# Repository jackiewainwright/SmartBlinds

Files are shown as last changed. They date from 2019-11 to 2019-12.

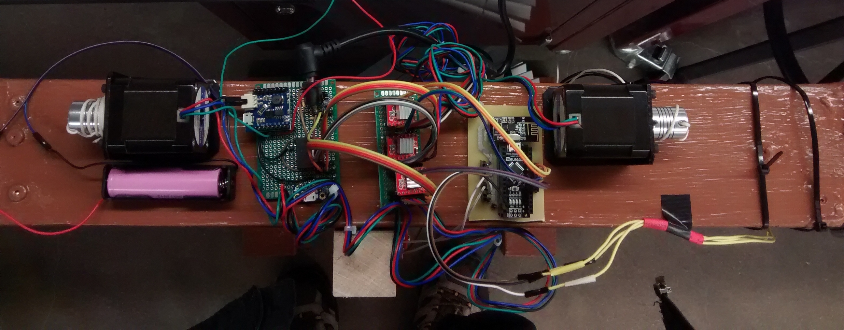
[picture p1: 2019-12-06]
hardware_photo.jpg

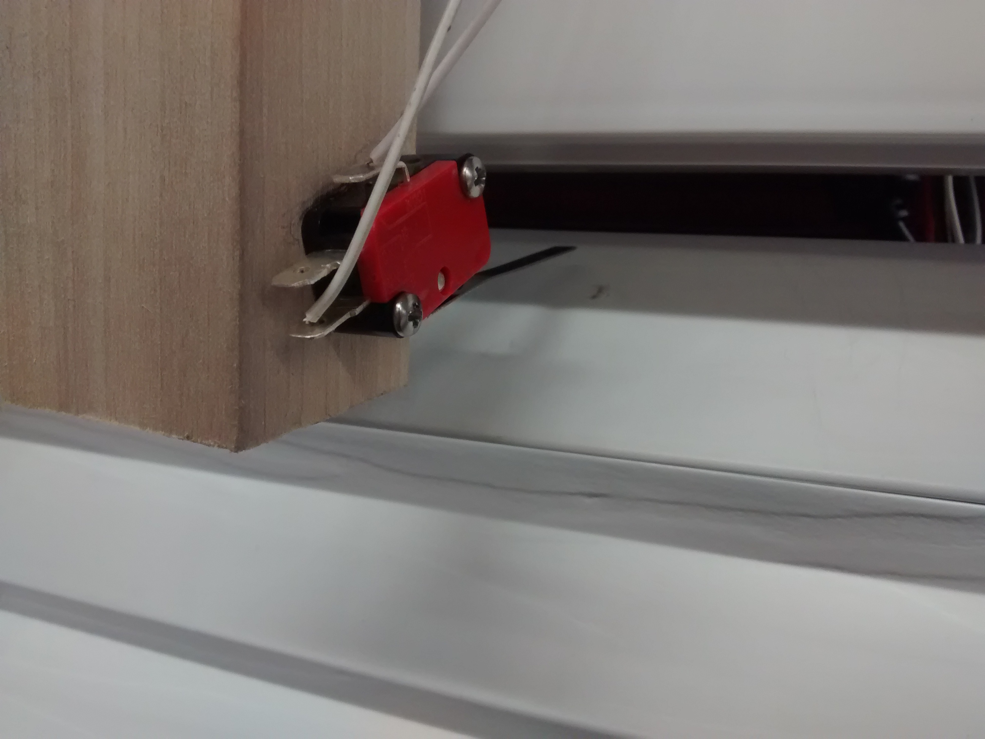
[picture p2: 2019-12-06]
switch_photo.jpg

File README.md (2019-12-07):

# SmartBlinds
A senior design project that has a mobile application that sends user preferences (time, light, temp) to a micro controller system. The micro controller system tells the blinds whether to go up or down based off input from the sensor subsystem. The micro controller controls the motors which raises blinds up/down and opens slats.

# Motors
File descriptions:
- motorhw: is an Eagle project that contains the PCB I printed. The PCB was only half used since it was printed before we switched motors. The half containing the Nano and transceiver is used, while the half containing motor drivers is unused. Pictures of the schematic and layouts are in motorhw\_schematic.png and motorhw\_layout.png. 
- hardware\_photo.jpg and switch\_photo.jpg: Pictures of the final products.
- motor\_demonstration.mov: Video of the blinds being lifted, lowered and rotated to their limits. 
- logic\_diagram.png and power\_diagram.png: Basic schematics made in Fritzing. These are kind of low-quality because I couldn't find files for every part. In the logic diagram, two jacks are shown; the top supplies 12V and the bottom supplies 5V. In the drivers, A1,A2,B1,B2 aren't connected; they each should be connected to a motor. In the power diagram, imagine the battery is a Li-Ion, replace the TP4056 with a TP5410, imagine it's on a protoboard instead of breadboard. 
- keiths\_program.ino: Program used by Keith on the nano. 
- my\_program.ino: Program used by me to develop and test the motor subsystem.
- additional_validation.pdf: Validation that I didn't put in the report. My bad

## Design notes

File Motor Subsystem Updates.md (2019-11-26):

9-25

Rough PCB design finished. However, we've decided to get a protoboard version working. For the final product, a protoboard will work. The only problem is reduced technical merit. 

9-30 

Finished proto board.

This proto board is split into 3 boards: nano board, motor board, and power board. 
* Nano board contains the nano, transceiver, multiple resistors for switches, and two transistors. 
* Motor board contains two motor drivers and three header rows providing an interface with the motors. 
* Power board contains the battery charger chip. It has headers connecting the battery, solar panel, and multiple power and ground connections. 

The nano board isn't soldered; it can easily, reliably, and more temporarily be connected with jumper wires. In the future, it may be soldered to become more reliable.

The motor board is fully soldered and tested, and it works.

The power board has the solar and battery components soldered. However, it doesn't have USB power connections soldered; this part may need minor design revisions first. 

Right now, we have a very solid option in the proto boards. There's no real need to get a PCB, except to increase technical merit and make it closer to a marketable product. 

10-14
We decided to change things up. The 28BYJs are pretty weak and lifting the blinds is too big a job for them. We bought NEMA-17s and drivers, and we'll use them to lift and probably rotate the blinds. 

10-22
Obtained the PCB finally. I got two copies in case one failed. The traces of one all work properly, so it seems like it'll work. I will solder female headers to attach the Nano and nRF transceiver. Currently I need surface-mount resistors, transistors, and capacitors, but if we go forward with the new motors the transistors and caps may not be necessary. 
If we replace the 28BYJ-48s with NEMA-17s, the right half of the board will be unnecessary, so I'll cut it off. 

10-27
Soldered power board together. 
Due to a miscommunication we didn't have a voltage booster chip. I bought a new battery-charging chip (TP5410) that boosts voltage as well. 

10-28
Tested the motor drivers. They can, in fact, run the motors. At max current, the drivers pull 12V 410mA, then deliver to the motor 1.05A per-phase. 

10-29
Soldered two motor drivers onto a protoboard. Put one motor on blinds, then tested whether it can lift half the blinds (successfully). Made video of motor lifting its share of blinds. 
The protoboard will be part of the final product. It'll have many jumpers connected to the power board and Arduino, but that's okay. The jumpers should be orderly enough to be more reliable than a breadboard. 

10-30
In lab, we drilled holes in the frame. One string is used for each side to lift the blinds, and they go through the holes to the top of the frame, where motors lift them. One shaft adaptor is put on each motor to attach the string.
It turned out we're missing a shaft adaptor, so we couldn't test rotation. We know it has enough torque because the 28BYJs did, and we'll implement this later. 

11-03
I accidentally burned out the battery charging board in a puff of smoke, so that's fun. However, I managed to test it enough to determine that the voltage boosting will be good enough (4.7V at 50mA), and it does charge the battery. I bought a new one and it'll ship on the 5th. 

11-19
The A4988 motor drivers burn out really easily, and I've had to buy 5 new ones. Made a new protoboard, fitted with female headers so I can add and replace driver boards whenever they burn out again.

11-24
Keith's motor program is complete and validated, and videos were made. The rotation is calibrated to within 5°.

11-25
The demo is tomorrow, and every part of the motor subsystem works.

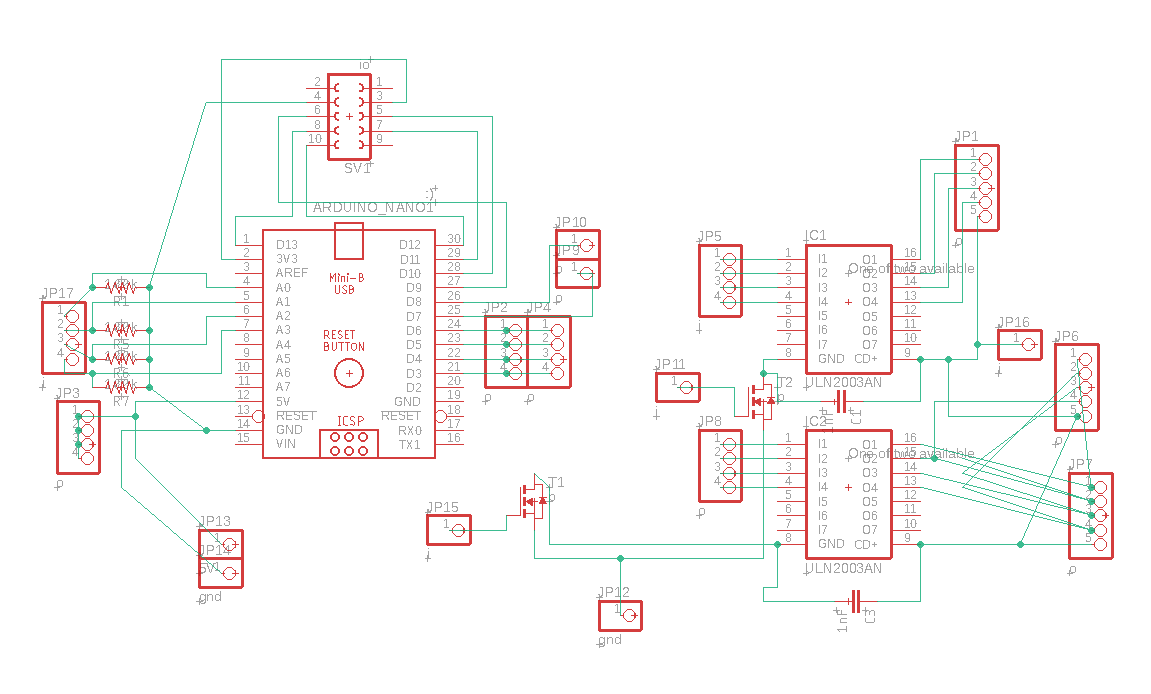
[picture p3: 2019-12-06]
motorhw_schematic.png

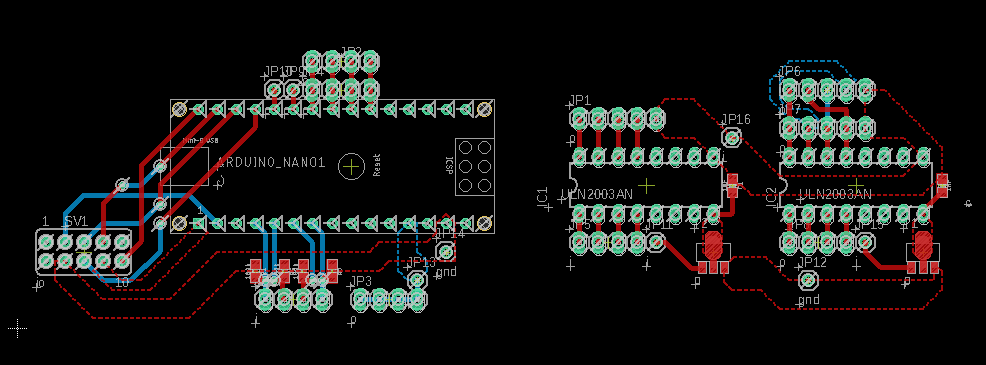
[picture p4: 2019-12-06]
motorhw_layout.png

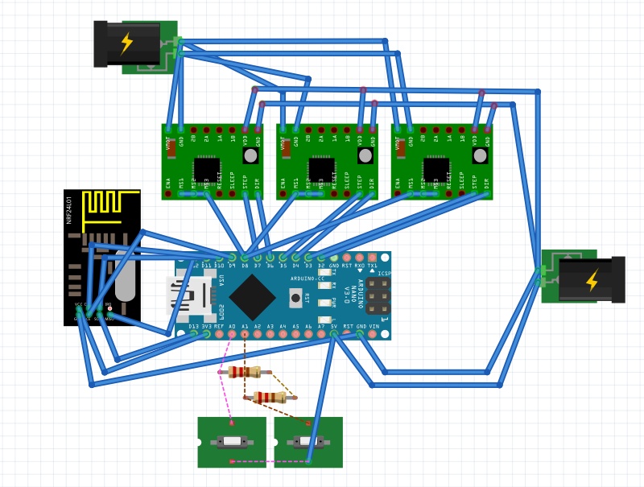
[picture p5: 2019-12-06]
logic_diagram.png

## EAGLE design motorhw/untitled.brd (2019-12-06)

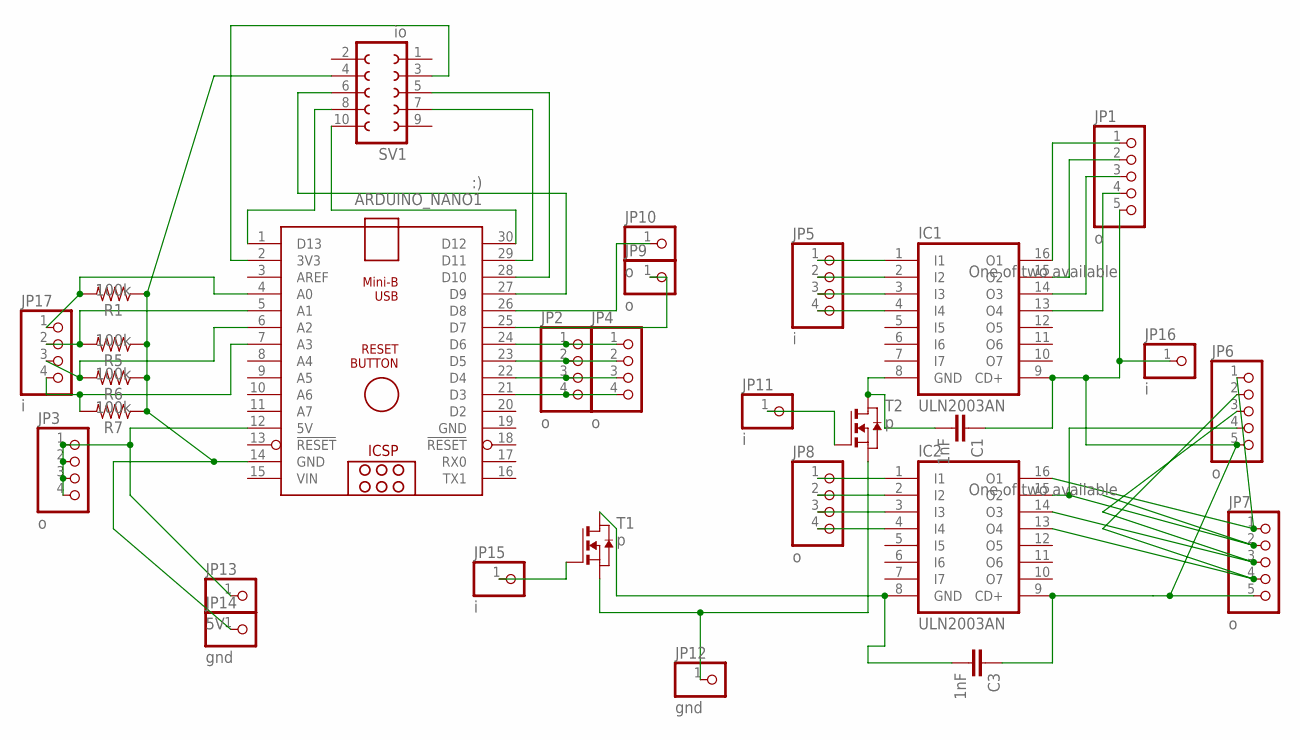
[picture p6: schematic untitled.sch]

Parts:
ARDUINO_NANO1: :); ARDUINO_NANO
C1, C3: 1nF; 0603
IC1, IC2: ULN2003AN; DIL16
JP1, JP6, JP7: o; 1X05
JP2, JP3, JP4, JP8: o; 1X04
JP5, JP17: i; 1X04
JP9, JP10: o; 1X01
JP11, JP15, JP16: i; 1X01
JP12, JP14: gnd; 1X01
JP13: 5V; 1X01
R1, R5, R6, R7: 100k; 0603
SV1: io; FE05-2
T1, T2: p; SOT89

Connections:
3V3: ARDUINO_NANO1.1 (D13), SV1.8
GND: ARDUINO_NANO1.19 (GND)
GND1: ARDUINO_NANO1.14 (GND), JP14.1, R1.1, R5.1, R6.1, R7.1, SV1.4
GND2: JP12.1, T1.3 (S), T2.3 (S)
LONGTHINGY: IC2.15 (O2), JP6.4, JP7.2
unnamed: ARDUINO_NANO1.4 (A0), JP17.1, R1.2
unnamed: ARDUINO_NANO1.21 (D3), JP2.4, JP4.4
unnamed: ARDUINO_NANO1.30 (D12), SV1.10
unnamed: IC2.16 (O1), JP6.1, JP7.1
unnamed: IC2.14 (O3), JP6.3, JP7.3
unnamed: IC2.13 (O4), JP6.2, JP7.4
unnamed: IC1.16 (O1), JP1.1
unnamed: IC1.15 (O2), JP1.2
unnamed: IC1.14 (O3), JP1.3
unnamed: IC1.13 (O4), JP1.4
unnamed: ARDUINO_NANO1.22 (D4), JP2.3, JP4.3
unnamed: ARDUINO_NANO1.25 (D7), JP9.1
unnamed: ARDUINO_NANO1.23 (D5), JP2.2, JP4.2
unnamed: ARDUINO_NANO1.29 (D11), SV1.7
unnamed: ARDUINO_NANO1.28 (D10), SV1.5
unnamed: ARDUINO_NANO1.27 (D9), SV1.6
unnamed: ARDUINO_NANO1.24 (D6), JP2.1, JP4.1
unnamed: ARDUINO_NANO1.2 (3V3), SV1.3
unnamed: IC1.1 (I1), JP5.1
unnamed: IC1.2 (I2), JP5.2
unnamed: IC1.3 (I3), JP5.3
unnamed: IC1.4 (I4), JP5.4
unnamed: IC2.1 (I1), JP8.1
unnamed: IC2.2 (I2), JP8.2
unnamed: IC2.3 (I3), JP8.3
unnamed: IC2.4 (I4), JP8.4
unnamed: ARDUINO_NANO1.26 (D8), JP10.1
unnamed: JP11.1, T2.1 (G)
unnamed: JP15.1, T1.1 (G)
unnamed: ARDUINO_NANO1.5 (A1), JP17.2, R5.2
unnamed: ARDUINO_NANO1.6 (A2), JP17.3, R6.2
unnamed: ARDUINO_NANO1.7 (A3), JP17.4, R7.2
ULN1GND: C1.2, IC1.8 (GND), T2.2 (D), T2.2@1 (D)
ULN2GND: C3.2, IC2.8 (GND), T1.2 (D), T1.2@1 (D)
VCC1: ARDUINO_NANO1.12 (5V), JP3.1, JP3.2, JP3.3, JP3.4, JP13.1
VCC2: C1.1, C3.1, IC1.9 (CD+), IC2.9 (CD+), JP1.5, JP6.5, JP7.5, JP16.1
VIN: ARDUINO_NANO1.15 (VIN)

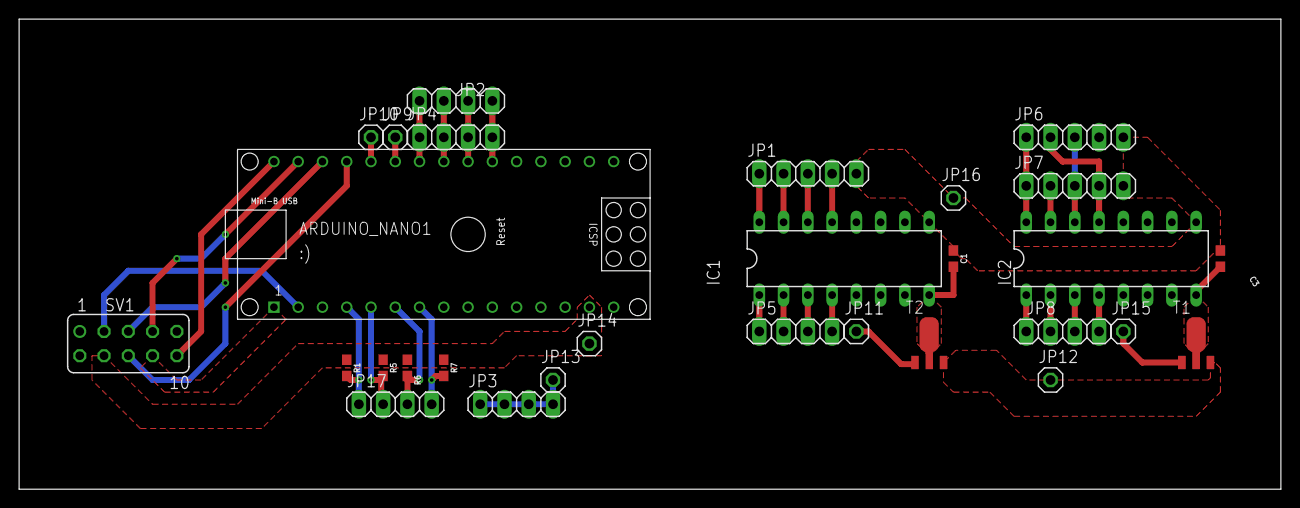
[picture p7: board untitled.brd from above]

Board: 2 copper layers, 132.1 x 49.2 mm, 29 parts (0 on the bottom side), 40 nets.

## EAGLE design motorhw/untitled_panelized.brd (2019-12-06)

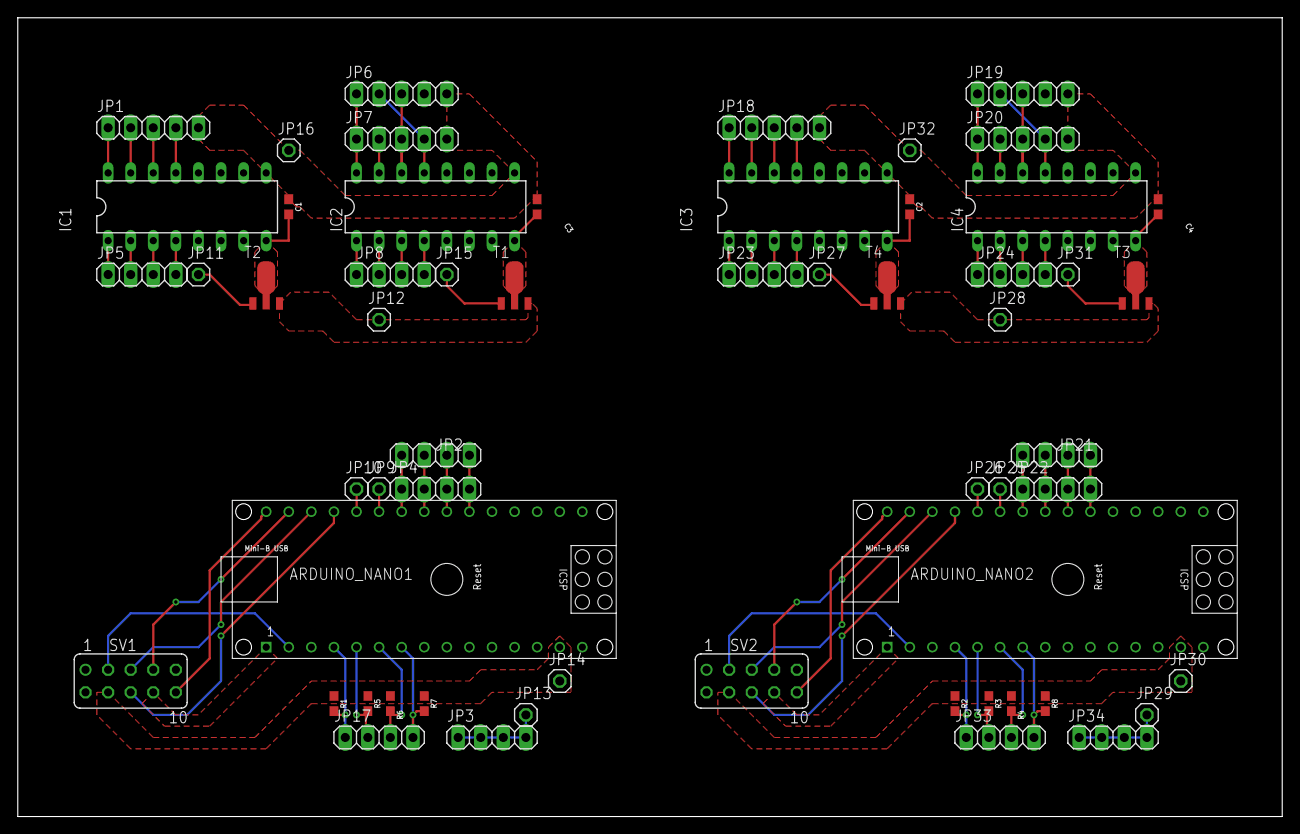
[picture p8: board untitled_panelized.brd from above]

Board: 2 copper layers, 142.2 x 89.8 mm, 58 parts (0 on the bottom side), 80 nets.

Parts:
ARDUINO_NANO1, ARDUINO_NANO2: ARDUINO_NANO
C1, C2, C3, C4: 1nF; 0603
IC1, IC2, IC3, IC4: ULN2003AN; DIL16
JP1, JP6, JP7, JP18, JP19, JP20: 1X05
JP2, JP3, JP4, JP5, JP8, JP17, JP21, JP22, JP23, JP24, JP33, JP34: 1X04
JP9, JP10, JP11, JP12, JP13, JP14, JP15, JP16, JP25, JP26, JP27, JP28, JP29, JP30, JP31, JP32: 1X01
R1, R2, R3, R4, R5, R6, R7, R8: 100k; 0603
SV1, SV2: FE05-2
T1, T2, T3, T4: SOT89

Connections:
3V1: ARDUINO_NANO2.1, SV2.8
3V3: ARDUINO_NANO1.1, SV1.8
GND1: ARDUINO_NANO1.14, JP14.1, R1.1, R5.1, R6.1, R7.1, SV1.4
GND2: JP12.1, T1.3, T2.3
GND4: ARDUINO_NANO2.14, JP30.1, R2.1, R3.1, R4.1, R8.1, SV2.4
GND5: JP28.1, T3.3, T4.3
LONGTHINGY: IC2.15, JP6.4, JP7.2
LONGTHINGY1: IC4.15, JP19.4, JP20.2
unnamed: ARDUINO_NANO1.4, JP17.1, R1.2
unnamed: ARDUINO_NANO2.4, JP33.1, R2.2
unnamed: ARDUINO_NANO1.21, JP2.4, JP4.4
unnamed: ARDUINO_NANO1.30, SV1.10
unnamed: IC4.16, JP19.1, JP20.1
unnamed: IC2.16, JP6.1, JP7.1
unnamed: IC4.14, JP19.3, JP20.3
unnamed: IC2.14, JP6.3, JP7.3
unnamed: IC2.13, JP6.2, JP7.4
unnamed: IC4.13, JP19.2, JP20.4
unnamed: IC1.16, JP1.1
unnamed: IC1.15, JP1.2
unnamed: IC1.14, JP1.3
unnamed: IC1.13, JP1.4
unnamed: ARDUINO_NANO1.22, JP2.3, JP4.3
unnamed: IC3.16, JP18.1
unnamed: ARDUINO_NANO1.25, JP9.1
unnamed: ARDUINO_NANO1.23, JP2.2, JP4.2
unnamed: IC3.15, JP18.2
unnamed: IC3.14, JP18.3
unnamed: ARDUINO_NANO1.29, SV1.7
unnamed: ARDUINO_NANO1.28, SV1.5
unnamed: ARDUINO_NANO1.27, SV1.6
unnamed: ARDUINO_NANO1.24, JP2.1, JP4.1
unnamed: ARDUINO_NANO1.2, SV1.3
unnamed: IC3.13, JP18.4
unnamed: IC1.1, JP5.1
unnamed: IC1.2, JP5.2
unnamed: IC1.3, JP5.3
unnamed: IC1.4, JP5.4
unnamed: IC2.1, JP8.1
unnamed: IC2.2, JP8.2
unnamed: IC2.3, JP8.3
unnamed: IC2.4, JP8.4
unnamed: ARDUINO_NANO1.26, JP10.1
unnamed: JP11.1, T2.1
unnamed: JP15.1, T1.1
unnamed: ARDUINO_NANO2.30, SV2.10
unnamed: ARDUINO_NANO1.5, JP17.2, R5.2
unnamed: ARDUINO_NANO1.6, JP17.3, R6.2
unnamed: ARDUINO_NANO1.7, JP17.4, R7.2
unnamed: ARDUINO_NANO2.29, SV2.7
unnamed: ARDUINO_NANO2.28, SV2.5
unnamed: ARDUINO_NANO2.27, SV2.6
unnamed: ARDUINO_NANO2.2, SV2.3
unnamed: ARDUINO_NANO2.21, JP21.4, JP22.4
unnamed: ARDUINO_NANO2.22, JP21.3, JP22.3
unnamed: ARDUINO_NANO2.23, JP21.2, JP22.2
unnamed: ARDUINO_NANO2.24, JP21.1, JP22.1
unnamed: IC3.1, JP23.1
unnamed: IC3.2, JP23.2
unnamed: IC3.3, JP23.3
unnamed: IC3.4, JP23.4
unnamed: IC4.1, JP24.1
unnamed: IC4.2, JP24.2
unnamed: IC4.3, JP24.3
unnamed: IC4.4, JP24.4
unnamed: ARDUINO_NANO2.25, JP25.1
unnamed: ARDUINO_NANO2.26, JP26.1
unnamed: JP27.1, T4.1
unnamed: JP31.1, T3.1
unnamed: ARDUINO_NANO2.5, JP33.2, R3.2
unnamed: ARDUINO_NANO2.6, JP33.3, R4.2
unnamed: ARDUINO_NANO2.7, JP33.4, R8.2
ULN1GND: C1.2, IC1.8, T2.2, T2.2@1
ULN1GND1: C2.2, IC3.8, T4.2, T4.2@1
ULN2GND: C3.2, IC2.8, T1.2, T1.2@1
ULN2GND1: C4.2, IC4.8, T3.2, T3.2@1
VCC1: ARDUINO_NANO1.12, JP3.1, JP3.2, JP3.3, JP3.4, JP13.1
VCC2: C1.1, C3.1, IC1.9, IC2.9, JP1.5, JP6.5, JP7.5, JP16.1
VCC3: C2.1, C4.1, IC3.9, IC4.9, JP18.5, JP19.5, JP20.5, JP32.1
VCC4: ARDUINO_NANO2.12, JP29.1, JP34.1, JP34.2, JP34.3, JP34.4

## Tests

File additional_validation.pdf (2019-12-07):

Additional Validation

This document contains some validation that didn’t make its way into the report. It includes power source output values and motor ranges.
One issue is that the 5V output of the battery charger output falls if it’s charging the battery. If it has a battery connected it outputs 5V, if it’s just a charge input it outputs 5.1V, but if both are connected it falls significantly. If the charger is a USB input from the wall it reaches around 4.2V, while if it’s a 150mA solar charger or DC power supply it outputs 3.5V, which is less than the battery voltage. This is a strange design flaw in the charger chip, especially since the manufacturer promises that it’s okay to connect a load while charging. It also wasn’t caught early, and if it was then a separate boost converter would’ve been used.
System Requirements | Specification | Actual | Form of measurement | Progress
Boot to Communication Time | 10 seconds | 5 sec | Timer | Complete
Rotation Range | 120 degrees | 160 degrees | Observation | Complete
Lift Range | frame height | frame height | Observation | Complete
Full Rotation Duration | < 20 sec | 9 sec | Timer | Complete
Full Lift Duration | < 20 sec | 15 sec | Timer | Complete
Limit Switch Feedback | 100% reliable | 100% reliable | Repeated Testing | Complete
Battery Supply under Load | > 4.8 V | 4.85 V | Voltmeter | Complete
12V Supply under Load | > 11 V | 12.32V | Voltmeter | Complete
Charger Current Supply (>4.8V) | > 250 mA | 350 mA | Voltmeter, resistors | Complete
Battery Supply While Charging | > 4.8 V | 3.5V-4.2V, depending on charger power | Voltmeter | Incomplete

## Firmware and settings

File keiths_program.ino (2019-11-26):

//________________________________________________________________________________________________________________
//  This module is for the motor arduino and is responsible for the following actions:
//          - using motor drivers to power the NEMA-17 steppers
//          - using limit switches to know the lower and upper bounds of the height of blinds
//          - using a limit switch to know the upper bound of the slat angle
//          - receive a signal from the ESP32 and the Sensory subsytems that tells the motors what to do
//________________________________________________________________________________________________________________

#include <math.h>

//include the libraries for the needed hardware components
#include <SPI.h>
#include <nRF24L01.h>
#include <RF24.h>
//#include <Adafruit_GFX.h>
#include <Wire.h>
//#include <Adafruit_ILI9341.h>
//#include <Adafruit_STMPE610.h>

//initialize the parts for the nRF24L01
RF24 radio(9, 10); // CE, CSN                                          depends on the pinout of the nano
const byte ESP_address[6] = "10011";              // ESP address for receiving state mode
const byte Sensor_Address[6] = "00001";           // Sensor address for receiving temp and light values

//set up code for the received array and loop
//__________________________________________________________________________
float Sensor_Data[8];
float ESP_Data[4];

float temp_error; float light_error; float temperature; float light; 
float temp_angle; float temp_height; float light_angle; float light_height;

int t = 0; 
int p = 0;
int x = 0;
int y = 0;
int a = 0;

// Initial angle is kind of confusing. Higher angle moves toward the switch. The switch is at 90, but it should be double the initial movement.. Was I wrong? No, I merely flipped every angle. Should some angles be flipped?
float HeightStateP[] = { 0 , 0 };    // 0 means fully lowered
float AngleStateP[] = { 0 , 0 };    // 20 degree slat angle starting out  (I'd say 0 if you want it perpendicular)
float HeightStateT[] = { 0 , 0 };    // 0 means fully lowered
float AngleStateT[] = { 0 , 0 };    // 20 degree slat angle starting out

float AngleDiff;
float HeightDiff;

float StateSelect; float Manual_HeightState;
//__________________________________________________________________________

/*
//include for stepper drivers
#include "A4988.h"
#define MOTOR_STEPS 200
#define DIR1 8
#define STEP1 7
#define OPPDIR 9
#define DIR2 11
#define STEP2 10
#define MS1 6                                                                     //currently commented out because I want to try the other more accurate way of driving the stepper motors
#define MS2 5  
#define MS3 4  
#define EN1 3
#define EN2 2
A4988 stepper1(MOTOR_STEPS, DIR1, STEP1, EN1, MS1, MS2, MS3);
A4988 stepper2(MOTOR_STEPS, DIR2, STEP2, EN2, MS1, MS2, MS3);
*/

//stuff for limit switches
#define LimitSwitchTop 2                                                          // switch at the top of blinds 
#define LimitSwitchBottom 1                                                       // switch at the bottom of blinds

#define LIFTDELAY 400 
#define ROTDELAY 2000

#define MULT 1.038


/*  Peter's directions:
    For lifting, just do it trial and error honestly, it's easy to switch and hard to specify in text. 
    For rotating, LOW is toward switch. HIGH is outward.
    Steps: For x degrees, rotate 16*x*200/360 steps. 
    Where I changed the step counts, I've stuck 16* on it. 
    Where I changed rotating direction, I've commented with b.
    I also changed delays to LIFTDELAY and ROTDELAY and increased them, and I changed the switch directions and values.
*/

//This is how I want to drive the stepper motors
//Stepper pins 1 and 2 are for the vertical raising of the blinds
//Stepper pins 3 are for the slat angle changes 
//--------------------------------------------------------
// defines pins numbers
const int stepPin_1 = 2;          
const int dirPin_1 = 3;
const int stepPin_2 = 4; 
const int dirPin_2 = 5;
const int stepPin_3 = 6; 
const int dirPin_3 = 7;

float numSteps;
//--------------------------------------------------------


// Resets the blinds. End up lowered all the way and rotated to switch.
// Proposed changes: if the switch starts pressed, rotate a certain amount to unpress the switch first
void startup() {
  //blinds boot up by hitting the limit switches for bottom of blinds and the slat angle to begin in the same orientation each time
  Serial.println("Going to bottom");
  while (analogRead(LimitSwitchBottom) >= 800){
    digitalWrite(dirPin_1,HIGH);
    digitalWrite(dirPin_2,HIGH);
    digitalWrite(stepPin_1,HIGH);
    digitalWrite(stepPin_2,HIGH); 
    delayMicroseconds(LIFTDELAY); 
    digitalWrite(stepPin_1,LOW); 
    digitalWrite(stepPin_2,LOW);
    delayMicroseconds(LIFTDELAY);                                                            // delay can be reduced or removed to improve performance
  }
  Serial.println("Rotating to beginning");
  while (analogRead(LimitSwitchTop) >= 800){
    digitalWrite(dirPin_3,LOW);     // b
    digitalWrite(stepPin_3,HIGH);
    delayMicroseconds(ROTDELAY); 
    digitalWrite(stepPin_3,LOW); 
    delayMicroseconds(ROTDELAY);                                                                 // delay can be reduced or removed to improve performance
  }  

  // Initial angle is 60. Angle to step multiplier is 16*1.11
  for(int x = 0; x < 16*MULT*60; x++) {   
    digitalWrite(dirPin_3,HIGH);    // b
    digitalWrite(stepPin_3,HIGH); 
    delayMicroseconds(ROTDELAY); 
    digitalWrite(stepPin_3,LOW); 
    delayMicroseconds(ROTDELAY);
  }
}


void setup() {
  // put your setup code here, to run once:
  //--------------------------------------------------------
  // Sets the two pins for each stepper as Outputs
  pinMode(stepPin_1,OUTPUT); 
  pinMode(dirPin_1,OUTPUT);
  pinMode(stepPin_2,OUTPUT); 
  pinMode(dirPin_2,OUTPUT);
  pinMode(stepPin_3,OUTPUT); 
  pinMode(dirPin_3,OUTPUT);

  pinMode(8,OUTPUT); // output LED for debug
  digitalWrite(8,HIGH);
  delay(100);
  digitalWrite(8,LOW);
  //--------------------------------------------------------  

  for(int x = 0; x < 5; x++) {   
    digitalWrite(dirPin_1,HIGH);
    digitalWrite(stepPin_1,HIGH);  
    digitalWrite(dirPin_2,HIGH);
    digitalWrite(stepPin_2,HIGH); 
    digitalWrite(dirPin_3,HIGH);
    digitalWrite(stepPin_3,HIGH); 
    delayMicroseconds(ROTDELAY); 
    digitalWrite(stepPin_1,LOW); 
    digitalWrite(stepPin_2,LOW); 
    digitalWrite(stepPin_3,LOW); 
    delayMicroseconds(ROTDELAY);
  }

  //setup code for initializing the radio
  Serial.begin(115200);
  Serial.println("Howdy");
  radio.begin();
  radio.openReadingPipe(0, Sensor_Address);                                              // this will read from radio signal from the ESP32
  radio.setPALevel(RF24_PA_MIN);
  radio.startListening();

  Serial.println("starting motor subsystem...\n");
}








int i=-1;  // debug, lets us change state every so often
int r = 0;
void loop() {
//  delay(32000);
  i++;
  delay(100);
  // put your main code here, to run repeatedly:

//________________________________________________________________________________
// receive the two sets of data from the App subsystem and the Sensors Subsystem  
//  radio.stopListening();
//  radio.openReadingPipe(0, Sensor_Address);
//  radio.setPALevel(RF24_PA_MIN);
//  radio.startListening();

//  if(radio.available()){ 
//    radio.read(&ESP_Data, sizeof(ESP_Data));
//
//    ManualState = ESP_Data[0];
//    TempState = ESP_Data[1];
//    PhotoState = ESP_Data[2];
//    Manual_HeightState = ESP_Data[3];
//
//    radio.stopListening();
//    radio.openReadingPipe(0, Sensor_address);                                              
//    radio.setPALevel(RF24_PA_MIN);
//    radio.startListening();
//    
    radio.startListening();

    if(radio.available()){
      radio.read(&Sensor_Data, sizeof(Sensor_Data));
      
      temperature = Sensor_Data[0];
      light = Sensor_Data[1];
      temp_angle = Sensor_Data[2] - 90;
      temp_height = Sensor_Data[3];
      light_angle = Sensor_Data[4] - 90;
      light_height = Sensor_Data[5];
      StateSelect = Sensor_Data[6];
      Manual_HeightState = Sensor_Data[7];
      
      Serial.println("Reveived Data: ");
      Serial.print(Sensor_Data[0]); Serial.print(" ");
      Serial.print(Sensor_Data[1]); Serial.print(" ");
      Serial.print(temp_angle); Serial.print(" ");
      Serial.print(Sensor_Data[3]); Serial.print(" ");
      Serial.print(light_angle); Serial.print(" ");
      Serial.print(Sensor_Data[5]); Serial.print(" ");
      Serial.print(Sensor_Data[6]); Serial.print(" ");
      Serial.print(Sensor_Data[7]); Serial.println(" ");
      
      //Serial.println(temperature);
      //Serial.println("available");
    } 

//  }
//__________________________________________________________________________________
//
//  if (i==0) {
//    Serial.println("i=0");
//    TempState = 1;
//    temp_angle = 60;
//  }
//
//  if (i==300) {
//    Serial.println("i=3");
//    temp_angle = 0;
//  }
//
//  if (i==600) {
//    Serial.println("i=6");
//    temp_angle = -60;
//  }
//
//  if (i==900) {
//    Serial.println("i=9");
//    temp_angle = 80;
//    temp_height = 1;
//  }
//
//  if(i==1200) {
//    Serial.println("i=12");
//    temp_height = 0;
//  }

// now to determine the angle and blind height difference 
    if(StateSelect == 1){  // should be 1
      Serial.println(" Temperature Mode Selected...");
      startup();
      // Debug: 
//      delay(1000);
//      digitalWrite(dirPin_3,HIGH);                  // b
//      numSteps = 16*round((45)*MULT); 
//      Serial.print("(never runs) negative rot numSteps: ");  // This line is odd, why is it here?
//      Serial.println(numSteps);
//      for(int x = 0; x < numSteps; x++) {
//        digitalWrite(stepPin_3,HIGH); 
//        delayMicroseconds(ROTDELAY); 
//        digitalWrite(stepPin_3,LOW); 
//        delayMicroseconds(ROTDELAY);
//      }
      a=0;
      while(StateSelect == 1){
        radio.startListening();

        if(radio.available()){
          radio.read(&Sensor_Data, sizeof(Sensor_Data));
          temperature = Sensor_Data[0];
          light = Sensor_Data[1];
          temp_angle = Sensor_Data[2] - 90;
          temp_height = Sensor_Data[3];
          light_angle = Sensor_Data[4] - 90;
          light_height = Sensor_Data[5];
          StateSelect = Sensor_Data[6];
          Manual_HeightState = Sensor_Data[7];
      
        Serial.println("Reveived Data: ");
        Serial.print(Sensor_Data[0]); Serial.print(" ");
        Serial.print(Sensor_Data[1]); Serial.print(" ");
        Serial.print(temp_angle); Serial.print(" ");
        Serial.print(Sensor_Data[3]); Serial.print(" ");
        Serial.print(light_angle); Serial.print(" ");
        Serial.print(Sensor_Data[5]); Serial.print(" ");
        Serial.print(Sensor_Data[6]); Serial.print(" ");
        Serial.print(Sensor_Data[7]); Serial.println(" ");
        }

        
      t++;
      if(t >= 1){
        t=0;
        //Serial.print("x=");  // debug
        //Serial.println(x);
        if(a == 0){   
          AngleStateT[1] = temp_angle;
          HeightStateT[1] = temp_height;
          a=1;
          AngleDiff = AngleStateT[1] - AngleStateT[0];
          HeightDiff = HeightStateT[1] - HeightStateT[0];
//          Serial.print("Approaching angle and height: ");
//          Serial.print(temp_angle);
//          Serial.print(" ");
//          Serial.print(temp_height);
//          Serial.print(" with changes: ");
//          Serial.print(AngleDiff);
//          Serial.print(" ");
//          Serial.println(HeightDiff);
          //--------------------------------------------------------
          if(AngleDiff < 0.0){
            digitalWrite(dirPin_3,HIGH);                  // b
            numSteps = 16*round((-AngleDiff)*MULT); 
            Serial.print("(never runs) negative rot numSteps: ");  // This line is odd, why is it here?
            Serial.println(numSteps);
            for(int x = 0; x < numSteps; x++) {
              digitalWrite(stepPin_3,HIGH); 
              delayMicroseconds(ROTDELAY); 
              digitalWrite(stepPin_3,LOW); 
              delayMicroseconds(ROTDELAY);
            }
          }
          else if(AngleDiff > 0.0){
            digitalWrite(dirPin_3,LOW);                   // b
            numSteps = 16*round((AngleDiff)*MULT);   
            Serial.print("positive rot numSteps: ");
            Serial.println(numSteps);            
            for(int x = 0; x < numSteps; x++) {
              digitalWrite(stepPin_3,HIGH); 
              delayMicroseconds(ROTDELAY); 
              digitalWrite(stepPin_3,LOW); 
              delayMicroseconds(ROTDELAY);
            }
          
          }
          else if(AngleDiff = 0.0){
            //do nothing because no angle change
          }
          if(HeightDiff > 0.0){
            digitalWrite(dirPin_1,LOW);
            digitalWrite(dirPin_2,LOW);
            Serial.println("(never runs) going up");
            while(analogRead(LimitSwitchTop) >= 800){
              digitalWrite(stepPin_1,HIGH);
              digitalWrite(stepPin_2,HIGH); 
              delayMicroseconds(LIFTDELAY); 
              digitalWrite(stepPin_1,LOW);
              digitalWrite(stepPin_2,LOW); 
              delayMicroseconds(LIFTDELAY);
            }
          }
          else if(HeightDiff < 0.0){
            digitalWrite(dirPin_1,HIGH);
            digitalWrite(dirPin_2,HIGH);
            Serial.println("going down");
            while(analogRead(LimitSwitchBottom) >= 800){
              digitalWrite(stepPin_1,HIGH);
              digitalWrite(stepPin_2,HIGH); 
              delayMicroseconds(LIFTDELAY); 
              digitalWrite(stepPin_1,LOW); 
              digitalWrite(stepPin_2,LOW);
              delayMicroseconds(LIFTDELAY);
            }
          }
          else if(HeightDiff = 0.0){
            //do nothing, aka no change
          }
        
          //--------------------------------------------------------
        }
        else if(a == 1){
          AngleStateT[0] = temp_angle;
          HeightStateT[0] = temp_height;
          a=0;
          AngleDiff = AngleStateT[0] - AngleStateT[1];
          HeightDiff = HeightStateT[0] - HeightStateT[1];

          //--------------------------------------------------------
          if(AngleDiff < 0.0){
            digitalWrite(dirPin_3,HIGH);                // b
            numSteps = 16*round((-AngleDiff)*MULT);
            Serial.print("negative rot numSteps: ");
            Serial.println(numSteps);
            for(int x = 0; x < numSteps; x++) {
              digitalWrite(stepPin_3,HIGH); 
              delayMicroseconds(ROTDELAY); 
              digitalWrite(stepPin_3,LOW); 
              delayMicroseconds(ROTDELAY);
            }
          }
          else if(AngleDiff > 0.0){
            digitalWrite(dirPin_3,LOW);                 // b
            numSteps = 16*round((AngleDiff)*MULT);
            Serial.print("(never runs) positive rot numSteps: ");
            Serial.println(numSteps);
            for(int x = 0; x < numSteps; x++) {
              digitalWrite(stepPin_3,HIGH); 
              delayMicroseconds(ROTDELAY); 
              digitalWrite(stepPin_3,LOW); 
              delayMicroseconds(ROTDELAY);
            }
          
          }
          else if(AngleDiff = 0.0){
            //do nothing because no angle change
          }
          if(HeightDiff > 0.0){
            digitalWrite(dirPin_1,LOW);
            digitalWrite(dirPin_2,LOW);
            Serial.println("going up");
            while(analogRead(LimitSwitchTop) >= 800){
              digitalWrite(stepPin_1,HIGH);
              digitalWrite(stepPin_2,HIGH); 
              delayMicroseconds(LIFTDELAY); 
              digitalWrite(stepPin_1,LOW);
              digitalWrite(stepPin_2,LOW); 
              delayMicroseconds(LIFTDELAY);
            }
          }
          else if(HeightDiff < 0.0){
            digitalWrite(dirPin_1,HIGH);
            digitalWrite(dirPin_2,HIGH);
             Serial.println("(never runs) going down");
            while(analogRead(LimitSwitchBottom) >= 800){
              digitalWrite(stepPin_1,HIGH);
              digitalWrite(stepPin_2,HIGH); 
              delayMicroseconds(LIFTDELAY); 
              digitalWrite(stepPin_1,LOW); 
              digitalWrite(stepPin_2,LOW);
              delayMicroseconds(LIFTDELAY);
            }
          }
          else if(HeightDiff = 0.0){
            //do nothing, aka no change
          }
          //--------------------------------------------------------
        }
      }
       
      }
    }

    else if(StateSelect == 2){  // should be 2
            Serial.println(" Light Mode Selected...");

      startup();
      y=0;
      while(StateSelect == 2){
        
         radio.startListening();
        if(radio.available()){
          radio.read(&Sensor_Data, sizeof(Sensor_Data));
          temperature = Sensor_Data[0];
          light = Sensor_Data[1];
          temp_angle = Sensor_Data[2] - 90;
          temp_height = Sensor_Data[3];
          light_angle = Sensor_Data[4] - 90;
          light_height = Sensor_Data[5];
          StateSelect = Sensor_Data[6];
          Manual_HeightState = Sensor_Data[7];

          Serial.println("Reveived Data: ");
        Serial.print(Sensor_Data[0]); Serial.print(" ");
        Serial.print(Sensor_Data[1]); Serial.print(" ");
        Serial.print(temp_angle); Serial.print(" ");
        Serial.print(Sensor_Data[3]); Serial.print(" ");
        Serial.print(light_angle); Serial.print(" ");
        Serial.print(Sensor_Data[5]); Serial.print(" ");
        Serial.print(Sensor_Data[6]); Serial.print(" ");
        Serial.print(Sensor_Data[7]); Serial.println(" ");
        }
        p++;
      if(p >= 1){
        p=0;
        if(y == 0){
          AngleStateP[1] = light_angle;
          HeightStateP[1] = light_height;
          y=1;
          AngleDiff = AngleStateP[1] - AngleStateP[0];
          HeightDiff = HeightStateP[1] - HeightStateP[0];

          //--------------------------------------------------------
          if(AngleDiff < 0.0){
            digitalWrite(dirPin_3,HIGH);                // b
            numSteps = 16*round((-AngleDiff)*MULT);
            Serial.print("negative rot numSteps: ");
            Serial.println(numSteps);
            for(int x = 0; x < numSteps; x++) {
              digitalWrite(stepPin_3,HIGH); 
              delayMicroseconds(ROTDELAY); 
              digitalWrite(stepPin_3,LOW); 
              delayMicroseconds(ROTDELAY);
            }
          }
          else if(AngleDiff > 0.0){
            digitalWrite(dirPin_3,LOW);                 // b
            numSteps = 16*round((AngleDiff)*MULT);
            Serial.print("positive rot numSteps: ");
            Serial.println(numSteps);            
            for(int x = 0; x < numSteps; x++) {
              digitalWrite(stepPin_3,HIGH); 
              delayMicroseconds(ROTDELAY); 
              digitalWrite(stepPin_3,LOW); 
              delayMicroseconds(ROTDELAY);
            }
          
          }
          else if(AngleDiff = 0.0){
            //do nothing because no angle change
          }
          if(HeightDiff > 0.0){
            digitalWrite(dirPin_1,LOW);
            digitalWrite(dirPin_2,LOW);
            while(analogRead(LimitSwitchTop) >= 800){
              digitalWrite(stepPin_1,HIGH);
              digitalWrite(stepPin_2,HIGH); 
              delayMicroseconds(LIFTDELAY); 
              digitalWrite(stepPin_1,LOW);
              digitalWrite(stepPin_2,LOW); 
              delayMicroseconds(LIFTDELAY);
            }
          }
          else if(HeightDiff < 0.0){
            digitalWrite(dirPin_1,HIGH);
            digitalWrite(dirPin_2,HIGH);
            while(analogRead(LimitSwitchBottom) >= 800){
              digitalWrite(stepPin_1,HIGH);
              digitalWrite(stepPin_2,HIGH); 
              delayMicroseconds(LIFTDELAY); 
              digitalWrite(stepPin_1,LOW); 
              digitalWrite(stepPin_2,LOW);
              delayMicroseconds(LIFTDELAY);
            }
          }
          else if(HeightDiff = 0.0){
            //do nothing, aka no change
          }
          //-------------------------------------------------------------

        
        }
        else if(y == 1){
          AngleStateP[0] = light_angle;
          HeightStateP[0] = light_height;
          y=0;
          AngleDiff = AngleStateP[0] - AngleStateP[1];
          HeightDiff = HeightStateP[0] - HeightStateP[1];
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

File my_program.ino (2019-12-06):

/***
 * Idea for new feature: Both top motors use the same pins. 
 * Problem: Motors need to warm up before running. Touching the heatsinks helps? Observing voltages with multimeter helps?
 * 
 */

// This file was made by Laurentiu Badea. It's hosted somewhere on Github.
#include "A4988.h"

#define MOTOR_STEPS 200
#define DIR1 4
#define STEP1 3
#define DIR2 5
#define STEP2 6
#define MS1 2  // Unused, the MSx pins are all connected to VCC
#define MS2 2
#define MS3 2
// These two may not be connected. 
#define EN1 1
#define EN2 1

#define SWITCHB 1
#define SWITCHT 2
#define SWITCHR 2
// This monitors 12V supply. It's either 0 or 3.22V. 
#define POWERMONITOR 5

// Stepper+ 1: Both raising motors. Both are always active (except for a physical glitch) at the same time. 
// One motor rotates the opposite direction, which is fine.
// If these motors go too far up, they start skipping, which is ok. If they go too far down, they start raising again. 
// There's two switches, one at the bottom and one at the top. This is SWITCHB and SWITCHT (bottom and top).
// Stepper 2: Rotating motor. This goes from 0 to ~150 degrees. 
// If the motor rotates too far, idk what happens. I'm kind of scared of that. Might break something. 
// There's one switch on one end. (Current plan is to share this with the upper raising switch.)
A4988 stepper1(MOTOR_STEPS, DIR1, STEP1, EN1, MS1, MS2, MS3);
A4988 stepper2(MOTOR_STEPS, DIR2, STEP2, EN2, MS1, MS2, MS3);

void setup() {
  Serial.begin(9600);
  // (rpm, microstep)
  // Microstep is always 16
  stepper1.begin(40,16);
  stepper2.begin(3,16);  
  delay(1000);
  stepper1.enable();
  stepper2.enable();
//  stepper1.disable();
  stepper1.rotate(10);
  stepper2.rotate(5);
  delay(1000);
  stepper1.rotate(-10);
  stepper2.rotate(-5);
//  delay(1000);
//  lift(30000);
//  delay(1000);
//  lift(30000);
//  delay(2000);
//  fall(30000);
//  delay(1000);
//  fall(30000);
}

void loop() {
  Serial.println("Howdy");
  delay(1000);
//  if (analogRead(SWITCHT)) < 128 { }
//  stepper1.rotate(10);
  lift(30000);
  delay(1000);
  fall(30000);
  delay(2000);
  rotf(300);
  delay(1000);
  rotr(210);
  delay(1000);
}

void lift(int n) {
  if ((n >= 10) && (analogRead(SWITCHT) > 300)) {
    stepper1.rotate(10);
    lift(n-10);
  }
}
void fall(int n) {
  if ((n >= 10) && (analogRead(SWITCHB) > 300)) {
    stepper1.rotate(-10);
    fall(n-10);    
  }
}

void rotr(int n) {
  if ((n >= 5)) {
    stepper2.rotate(5);
    rotr(n-5);
  }
}
void rotf(int n) {
  if ((n >= 5) && (analogRead(SWITCHR) > 300)) {
    stepper2.rotate(-5);
    rotf(n-5);
  }
}

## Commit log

2019-11-07 Adding program used to test, ft. comments to describe operation of motors
2019-11-26 Updates and Keith's motor program
2019-12-06 adding various files
    [DRILEGEND.CFG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]

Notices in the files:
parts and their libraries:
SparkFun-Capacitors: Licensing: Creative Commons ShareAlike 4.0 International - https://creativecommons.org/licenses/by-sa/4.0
